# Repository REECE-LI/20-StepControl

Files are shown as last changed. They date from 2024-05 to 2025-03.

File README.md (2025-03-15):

# 20步进电机闭环驱动



## 项目来源

项目参考了[XDrive](https://github.com/unlir/XDrive)和[稚晖君的Dummy](https://github.com/peng-zhihui/Dummy-Robot)内部的20步进电机工程。

固件是在稚晖君42步进电机（与20电机通用）的程序上改进的。

## 更新部分

此处与稚晖君版本的作比较。

1. MCU部分由STM32F103CBT6更换为STM32F303CCT6。

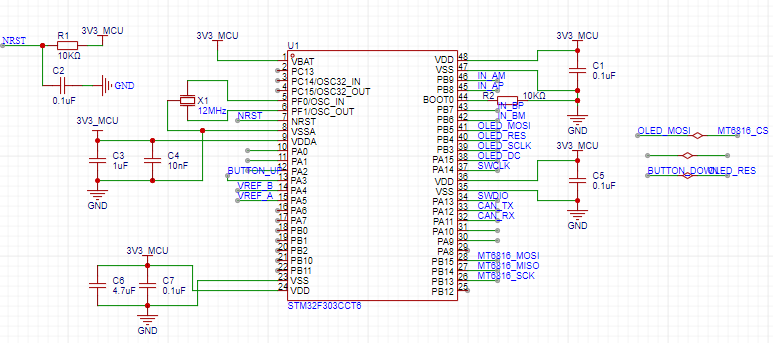
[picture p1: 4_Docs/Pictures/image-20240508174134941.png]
   

   - 内部flash翻倍（现在是256KB），原版的128KB在使用新版的`gcc`编译的时候会内存溢出（由于磁编码器需要校准，占用了32KB）。
   - 驱动器的电压控制直接使用DAC生成，不使用二阶低通滤波，硬件减少。
   - 由于flash翻倍了，可以在42步进电机上面增加一块Oled屏幕（XDrive上面有一块Oled屏幕，稚晖君版本上面预留了Oled的接口，但是flash已经完全用完了）。

2. DCDC部分直接降压到3.3V，取消LDO

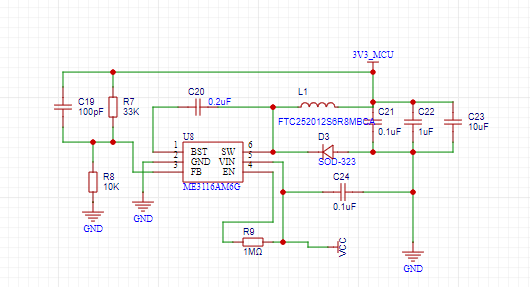
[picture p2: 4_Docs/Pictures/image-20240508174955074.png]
   

   - 没啥好说的。。。我就是懒得再焊LDO
   - Boost的自举电容需要0.2uF以上，原版使用了两个0402-0.1uF并联，这里直接使用0603-0.22uF，所占用面积差不多。
   - 分压电阻那可以再精细一点，当前输出的电压大约是3.4V。

3. CAN芯片由TJA1050更换为SIT3051

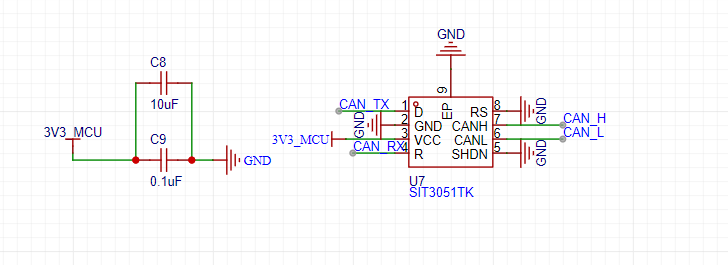
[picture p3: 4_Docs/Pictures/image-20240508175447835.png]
   

   - 小且便宜

## 使用

固件是在稚晖君的固件上面进行修改，使用Clion进行的烧写。（[Clion的教程在这里](https://zhuanlan.zhihu.com/p/145801160)）下载接口、电源接口、CAN接口都是焊盘连接。

- 按键按下通电程序会自动进行校准，校准完成后按下按键进入位置闭环，自动归零。
- 拨动开关是CAN信号120Ω的开关。
- 校准完后，我使用的是稚晖君的UltraLink里面的步进电机调试器，进行位置和速度的查看。（42步进电机版本加上了Oled屏幕可以直接查看）

- CAN信号控制指令可以在`can_base.cpp`中查看（如果有需要之后可以更新一下）

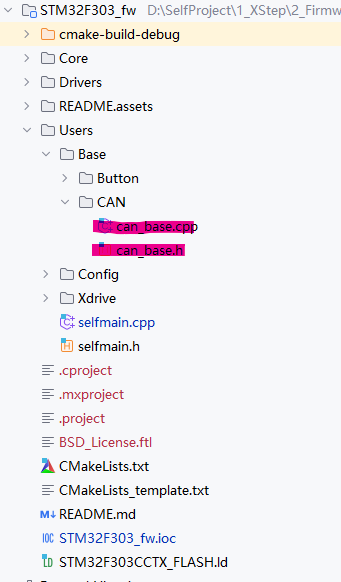
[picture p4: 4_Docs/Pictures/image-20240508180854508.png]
  

- 附一张42步进电机的驱动板，市面上的42步进闭环驱动其实很丰富了，张大头和创客都做的很好，后续再开（肯定不是因为懒）

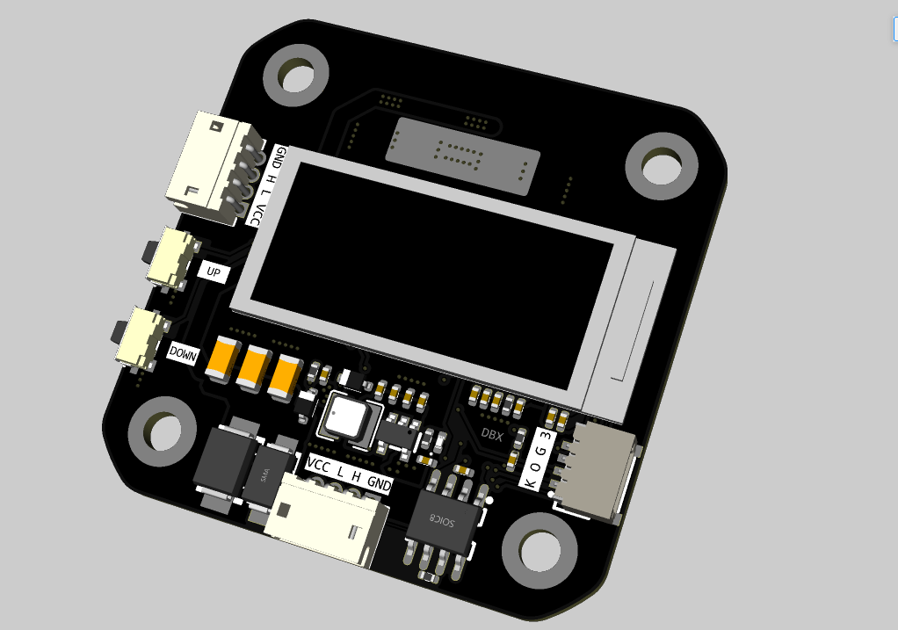
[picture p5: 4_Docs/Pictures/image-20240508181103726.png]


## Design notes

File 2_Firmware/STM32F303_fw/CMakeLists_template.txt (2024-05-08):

#THIS FILE IS AUTO GENERATED FROM THE TEMPLATE! DO NOT CHANGE!
set(CMAKE_SYSTEM_NAME Generic)
set(CMAKE_SYSTEM_VERSION 1)
cmake_minimum_required(VERSION 3.27)

# specify cross-compilers and tools
set(CMAKE_C_COMPILER arm-none-eabi-gcc)
set(CMAKE_CXX_COMPILER arm-none-eabi-g++)
set(CMAKE_ASM_COMPILER  arm-none-eabi-gcc)
set(CMAKE_AR arm-none-eabi-ar)
set(CMAKE_OBJCOPY arm-none-eabi-objcopy)
set(CMAKE_OBJDUMP arm-none-eabi-objdump)
set(SIZE arm-none-eabi-size)
set(CMAKE_TRY_COMPILE_TARGET_TYPE STATIC_LIBRARY)

# project settings
project(STM32F303_fw C CXX ASM)
set(CMAKE_CXX_STANDARD 17)
set(CMAKE_C_STANDARD 11)

#Uncomment for hardware floating point
#add_compile_definitions(ARM_MATH_CM4;ARM_MATH_MATRIX_CHECK;ARM_MATH_ROUNDING)
#add_compile_options(-mfloat-abi=hard -mfpu=fpv4-sp-d16)
#add_link_options(-mfloat-abi=hard -mfpu=fpv4-sp-d16)

#Uncomment for software floating point
#add_compile_options(-mfloat-abi=soft)

add_compile_options(-mcpu=cortex-m4 -mthumb -mthumb-interwork)
add_compile_options(-ffunction-sections -fdata-sections -fno-common -fmessage-length=0)

# uncomment to mitigate c++17 absolute addresses warnings
#set(CMAKE_CXX_FLAGS "${CMAKE_CXX_FLAGS} -Wno-register")

# Enable assembler files preprocessing
add_compile_options($<$<COMPILE_LANGUAGE:ASM>:-x$<SEMICOLON>assembler-with-cpp>)

if ("${CMAKE_BUILD_TYPE}" STREQUAL "Release")
    message(STATUS "Maximum optimization for speed")
    add_compile_options(-Ofast)
elseif ("${CMAKE_BUILD_TYPE}" STREQUAL "RelWithDebInfo")
    message(STATUS "Maximum optimization for speed, debug info included")
    add_compile_options(-Ofast -g)
elseif ("${CMAKE_BUILD_TYPE}" STREQUAL "MinSizeRel")
    message(STATUS "Maximum optimization for size")
    add_compile_options(-Os)
else ()
    message(STATUS "Minimal optimization, debug info included")
    add_compile_options(-Og -g)
endif ()

include_directories(Core/Inc Drivers/STM32F3xx_HAL_Driver/Inc
        Drivers/STM32F3xx_HAL_Driver/Inc/Legacy
        Drivers/CMSIS/Device/ST/STM32F3xx/Include
        Drivers/CMSIS/Include
        Users
        Users/Base/Button
        Users/Base/CAN
#        Users/Retarget
        Users/Xdrive
        Users/Xdrive/Driver
        Users/Xdrive/Encoder
        Users/Xdrive/Memory
        Users/Xdrive/Motor
        Users/Oled
)

add_definitions(-DDEBUG -DUSE_HAL_DRIVER -DSTM32F303xC)

file(GLOB_RECURSE SOURCES "Core/*.*" "Drivers/*.*" "Users/*.*")

set(LINKER_SCRIPT ${CMAKE_SOURCE_DIR}/STM32F303CCTX_FLASH.ld)

add_link_options(-Wl,-gc-sections,--print-memory-usage,-Map=${PROJECT_BINARY_DIR}/${PROJECT_NAME}.map)
add_link_options(-mcpu=cortex-m4 -mthumb -mthumb-interwork)
add_link_options(-T ${LINKER_SCRIPT})

add_executable(${PROJECT_NAME}.elf ${SOURCES} ${LINKER_SCRIPT})

set(HEX_FILE ${PROJECT_BINARY_DIR}/${PROJECT_NAME}.hex)
set(BIN_FILE ${PROJECT_BINARY_DIR}/${PROJECT_NAME}.bin)

add_custom_command(TARGET ${PROJECT_NAME}.elf POST_BUILD
        COMMAND ${CMAKE_OBJCOPY} -Oihex $<TARGET_FILE:${PROJECT_NAME}.elf> ${HEX_FILE}
        COMMAND ${CMAKE_OBJCOPY} -Obinary $<TARGET_FILE:${PROJECT_NAME}.elf> ${BIN_FILE}
        COMMENT "Building ${HEX_FILE}
Building ${BIN_FILE}")

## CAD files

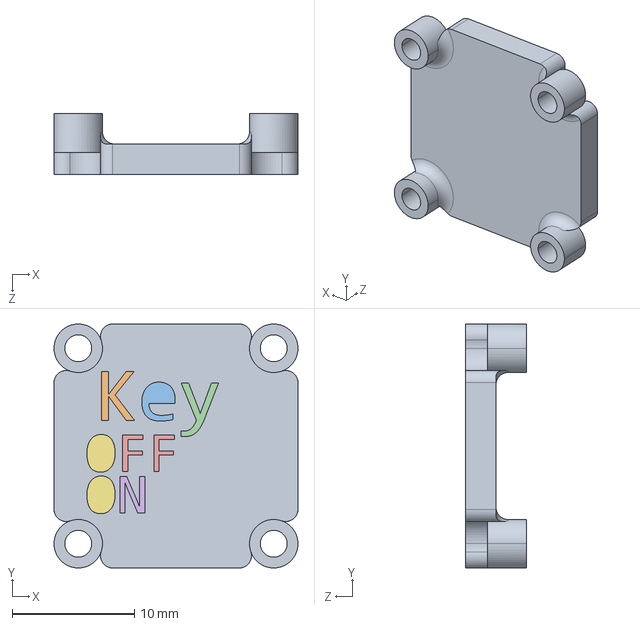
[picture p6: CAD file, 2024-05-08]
3_3Dmodels/20步进背板.STEP
20.0 x 20.0 x 5.00 mm

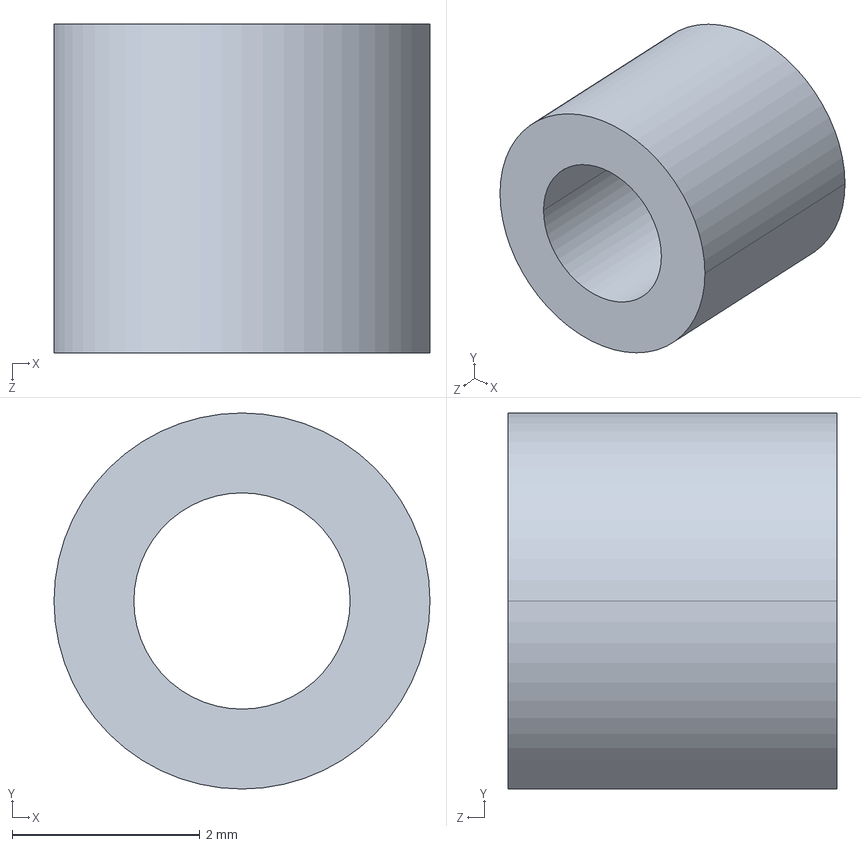
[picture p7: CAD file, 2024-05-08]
3_3Dmodels/20步进增高.STEP
4.00 x 4.00 x 3.50 mm

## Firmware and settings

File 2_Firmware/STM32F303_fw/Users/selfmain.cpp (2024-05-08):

#include "selfmain.h"


#include <cstdio>

#include "mt6816_stm32.h"
#include "tb67h450_stm32.h"

#include "button_stm32.h"
#include "configurations.h"
#include "can_base.h"


#include "encoder_calibrator_stm32.h"
#include "stockpile_f303cc.h"
#include "stockpile_config.h"


/*
TIM2通道 3 4进行DAC
TIM3 进行20kHZ中断
PB12 BTN_DOWN Key_1
 */

BoardConfig_t boardConfig;

Motor motor;
TB67H450 tb67H450;
MT6816 mt6816;
EncoderCalibrator encoderCalibrator(&motor);
Button button1(1, 1000);

void OnButton1Event(Button::Event _event);

void OnButton2Event(Button::Event _event);

void SelfMain() {

    //  读取配置 当前没有写
//    Stockpile_Flash_Data_Read_Data(&stockpile_data, &boardConfig, sizeof(BoardConfig_t));
    // use flash
    if (boardConfig.configStatus != CONFIG_OK) // use default settings
    {
        boardConfig = BoardConfig_t{
                .configStatus = CONFIG_OK,
                .canNodeId = 1,
                .encoderHomeOffset = 0,
                .defaultMode = Motor::MODE_COMMAND_VELOCITY,
                .currentLimit = 1 * 1000,    // A
                .velocityLimit = 1600 * motor.MOTOR_ONE_CIRCLE_SUBDIVIDE_STEPS, // r/s
                .velocityAcc = 100 * motor.MOTOR_ONE_CIRCLE_SUBDIVIDE_STEPS,   // r/s^2
                .calibrationCurrent=800,
                .dce_kp = 200,
                .dce_kv = 80,
                .dce_ki = 300,
                .dce_kd = 250,
                .enableMotorOnBoot=false,
                .enableStallProtect=false
        };

        Stockpile_Flash_Data_Write_Data16(&stockpile_data, (uint16_t *) &boardConfig, sizeof(BoardConfig_t));
    }
    // 加载板载数据
    motor.config.motionParams.encoderHomeOffset = boardConfig.encoderHomeOffset;
    motor.config.motionParams.ratedCurrent = boardConfig.currentLimit;
    motor.config.motionParams.ratedVelocity = boardConfig.velocityLimit;
    motor.config.motionParams.ratedVelocityAcc = boardConfig.velocityAcc;
    motor.motionPlanner.velocityTracker.SetVelocityAcc(boardConfig.velocityAcc);
    motor.motionPlanner.positionTracker.SetVelocityAcc(boardConfig.velocityAcc);
    motor.config.motionParams.caliCurrent = boardConfig.calibrationCurrent;
    motor.config.ctrlParams.dce.kp = boardConfig.dce_kp;
    motor.config.ctrlParams.dce.kv = boardConfig.dce_kv;
    motor.config.ctrlParams.dce.ki = boardConfig.dce_ki;
    motor.config.ctrlParams.dce.kd = boardConfig.dce_kd;
    motor.config.ctrlParams.stallProtectSwitch = boardConfig.enableStallProtect;

    /*---------------- Init Motor ----------------*/
    motor.AttachDriver(&tb67H450);
    motor.AttachEncoder(&mt6816);
    motor.controller->Init();
    motor.driver->Init();
    motor.encoder->Init();

    /*------------- Init peripherals -------------*/
    button1.SetOnEventListener(OnButton1Event);


    /*------- Start Close-Loop Control Tick ------*/
    CANInit(&hcan);
//    HAL_Delay(1);
    HAL_TIM_Base_Start_IT(&htim4);  // 100Hz
    HAL_TIM_Base_Start_IT(&htim3);  // 20kHz
//    HAL_Delay(1);
//
    if (button1.IsPressed() )
        encoderCalibrator.isTriggered = true;
    // 测试使用


    for (;;) {
        encoderCalibrator.TickMainLoop();
        if (boardConfig.configStatus == CONFIG_COMMIT) {
            boardConfig.configStatus = CONFIG_OK;
            // eeprom.put(0, boardConfig);
        } else if (boardConfig.configStatus == CONFIG_RESTORE) {
            // eeprom.put(0, boardConfig);
            HAL_NVIC_SystemReset();
        }

    }
}

void HAL_TIM_PeriodElapsedCallback(TIM_HandleTypeDef *htim) {
    if (htim->Instance == TIM3) {

        if (encoderCalibrator.isTriggered)
            encoderCalibrator.Tick20kHz();
        else
            motor.Tick20kHz();
    } else if (htim->Instance == TIM4) {
        button1.Tick(10);


    }
}


// button event
void OnButton1Event(Button::Event _event) {
    switch (_event) {
        case ButtonBase::UP:
            break;
        case ButtonBase::DOWN:
            break;
        case ButtonBase::LONG_PRESS:
//            HAL_NVIC_SystemReset();
            break;
        case ButtonBase::CLICK:
            motor.controller->SetCtrlMode(Motor::MODE_COMMAND_POSITION);
            break;
    }
}

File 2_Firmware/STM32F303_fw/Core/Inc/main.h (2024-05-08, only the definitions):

#define BUTTON_UP_Pin GPIO_PIN_3
#define BUTTON_UP_GPIO_Port GPIOA
#define VREF_A_Pin GPIO_PIN_4
#define VREF_A_GPIO_Port GPIOA
#define VREF_B_Pin GPIO_PIN_5
#define VREF_B_GPIO_Port GPIOA
#define MT6818_CLK_Pin GPIO_PIN_13
#define MT6818_CLK_GPIO_Port GPIOB
#define MT6816_MISO_Pin GPIO_PIN_14
#define MT6816_MISO_GPIO_Port GPIOB
#define MT6818_MOSI_Pin GPIO_PIN_15
#define MT6818_MOSI_GPIO_Port GPIOB
#define MT6816_CS_Pin GPIO_PIN_5
#define MT6816_CS_GPIO_Port GPIOB
#define BM_Pin GPIO_PIN_6
#define BM_GPIO_Port GPIOB
#define BP_Pin GPIO_PIN_7
#define BP_GPIO_Port GPIOB
#define AP_Pin GPIO_PIN_8
#define AP_GPIO_Port GPIOB
#define AM_Pin GPIO_PIN_9
#define AM_GPIO_Port GPIOB

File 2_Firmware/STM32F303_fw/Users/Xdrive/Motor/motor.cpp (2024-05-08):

#include "configurations.h"
#include "motor.h"

#include <cmath>


void Motor::Tick20kHz() {
    // 1.Encoder data Update
    encoder->UpdateAngle();

    // 2.Motor Control Update
    CloseLoopControlTick();
}


void Motor::AttachEncoder(EncoderBase *_encoder) {
    encoder = _encoder;
}


void Motor::AttachDriver(DriverBase *_driver) {
    driver = _driver;
}


void Motor::CloseLoopControlTick() {
    /************************************ First Called ************************************/
    static bool isFirstCalled = true;
    if (isFirstCalled) {
        int32_t angle;
        if (config.motionParams.encoderHomeOffset < MOTOR_ONE_CIRCLE_SUBDIVIDE_STEPS / 2) {
            angle =
                    encoder->angleData.rectifiedAngle >
                    config.motionParams.encoderHomeOffset + MOTOR_ONE_CIRCLE_SUBDIVIDE_STEPS / 2 ?
                    encoder->angleData.rectifiedAngle - MOTOR_ONE_CIRCLE_SUBDIVIDE_STEPS :
                    encoder->angleData.rectifiedAngle;
        } else {
            angle =
                    encoder->angleData.rectifiedAngle <
                    config.motionParams.encoderHomeOffset - MOTOR_ONE_CIRCLE_SUBDIVIDE_STEPS / 2 ?
                    encoder->angleData.rectifiedAngle + MOTOR_ONE_CIRCLE_SUBDIVIDE_STEPS :
                    encoder->angleData.rectifiedAngle;
        }

        controller->realLapPosition = angle;
        controller->realLapPositionLast = angle;
        controller->realPosition = angle;
        controller->realPositionLast = angle;

        isFirstCalled = false;
        return;
    }

    /********************************* Update Data *********************************/
    int32_t deltaLapPosition;

    // Read Encoder data
    controller->realLapPositionLast = controller->realLapPosition;
    controller->realLapPosition = encoder->angleData.rectifiedAngle;

    // Lap-Position calculate
    deltaLapPosition = controller->realLapPosition - controller->realLapPositionLast;
    if (deltaLapPosition > MOTOR_ONE_CIRCLE_SUBDIVIDE_STEPS >> 1)
        deltaLapPosition -= MOTOR_ONE_CIRCLE_SUBDIVIDE_STEPS;
    else if (deltaLapPosition < -MOTOR_ONE_CIRCLE_SUBDIVIDE_STEPS >> 1)
        deltaLapPosition += MOTOR_ONE_CIRCLE_SUBDIVIDE_STEPS;

    // Naive-Position calculate
    controller->realPositionLast = controller->realPosition;
    controller->realPosition += deltaLapPosition;

    /********************************* Estimate Data *********************************/
    // Estimate Velocity
    controller->estVelocityIntegral += (
            (controller->realPosition - controller->realPositionLast) * motionPlanner.CONTROL_FREQUENCY
            + ((controller->estVelocity << 5) - controller->estVelocity)
    );
    controller->estVelocity = controller->estVelocityIntegral >> 5;
    controller->estVelocityIntegral -= (controller->estVelocity << 5);

    // Estimate Position
    controller->estLeadPosition = Controller::CompensateAdvancedAngle(controller->estVelocity);
    controller->estPosition = controller->realPosition + controller->estLeadPosition;

    // Estimate Error
    controller->estError = controller->softPosition - controller->estPosition;

    /************************************ Ctrl Loop ************************************/
    if (controller->isStalled ||
        controller->softDisable ||
        !encoder->IsCalibrated()) {
        controller->ClearIntegral();    // clear integrals
        controller->focPosition = 0;    // clear outputs
        controller->focCurrent = 0;
        driver->Sleep();
    } else if (controller->softBrake) {
        controller->ClearIntegral();
        controller->focPosition = 0;
        controller->focCurrent = 0;
        driver->Brake();
    } else {
        switch (controller->modeRunning) {
            case MODE_STEP_DIR:
                controller->CalcDceToOutput(controller->softPosition, controller->softVelocity);
                break;
            case MODE_STOP:
                driver->Sleep();
                break;
            case MODE_COMMAND_Trajectory:
                controller->CalcDceToOutput(controller->softPosition, controller->softVelocity);
                break;
            case MODE_COMMAND_CURRENT:
                controller->CalcCurrentToOutput(controller->softCurrent);
                break;
            case MODE_COMMAND_VELOCITY:
                controller->CalcPidToOutput(controller->softVelocity);
                break;
            case MODE_COMMAND_POSITION:
                controller->CalcDceToOutput(controller->softPosition, controller->softVelocity);
                break;
            case MODE_PWM_CURRENT:
                controller->CalcCurrentToOutput(controller->softCurrent);
                break;
            case MODE_PWM_VELOCITY:
                controller->CalcPidToOutput(controller->softVelocity);
                break;
            case MODE_PWM_POSITION:
                controller->CalcDceToOutput(controller->softPosition, controller->softVelocity);
                break;
            default:
                break;
        }
    }

    /******************************* Mode Change Handle *******************************/
    if (controller->modeRunning != controller->requestMode) {
        controller->modeRunning = controller->requestMode;
        controller->softNewCurve = true;
    }

    /******************************* Update Hard-Goal *******************************/
    if (controller->goalVelocity > config.motionParams.ratedVelocity)
        controller->goalVelocity = config.motionParams.ratedVelocity;
    else if (controller->goalVelocity < -config.motionParams.ratedVelocity)
        controller->goalVelocity = -config.motionParams.ratedVelocity;
    if (controller->goalCurrent > config.motionParams.ratedCurrent)
        controller->goalCurrent = config.motionParams.ratedCurrent;
    else if (controller->goalCurrent < -config.motionParams.ratedCurrent)
        controller->goalCurrent = -config.motionParams.ratedCurrent;

    /******************************** Motion Plan *********************************/
    if ((controller->softDisable && !controller->goalDisable) ||
        (controller->softBrake && !controller->goalBrake)) {
        controller->softNewCurve = true;
    }

    if (controller->softNewCurve) {
        controller->softNewCurve = false;
        controller->ClearIntegral();
        controller->ClearStallFlag();
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

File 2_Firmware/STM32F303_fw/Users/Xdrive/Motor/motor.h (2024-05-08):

#ifndef CTRL_STEP_FW_MOTOR_H
#define CTRL_STEP_FW_MOTOR_H

#include "motion_planner.h"
#include "encoder_base.h"
#include "driver_base.h"


#ifdef __cplusplus
extern "C" {
#endif


class Motor
{
public:
    Motor() :
        controller(&controllerInstance)
    {
        /****************** Default Configs *******************/
        config.motionParams.encoderHomeOffset = 0;
        config.motionParams.caliCurrent = 2000;             // (mA)
        config.motionParams.ratedCurrent = 1000;            // (mA)
        config.motionParams.ratedCurrentAcc = 2 * 1000;     // (mA/s)
        config.motionParams.ratedVelocity = 30 * MOTOR_ONE_CIRCLE_SUBDIVIDE_STEPS;
        config.motionParams.ratedVelocityAcc = 1000 * MOTOR_ONE_CIRCLE_SUBDIVIDE_STEPS;

        config.ctrlParams.stallProtectSwitch = false;
        config.ctrlParams.pid =
            Controller::PID_t{
                .kp = 5,
                .ki = 30,
                .kd = 0
            };
        config.ctrlParams.dce =
            Controller::DCE_t{
                .kp = 200,
                .kv = 80,
                .ki = 300,
                .kd = 250
            };

        /*****************************************************/


        motionPlanner.AttachConfig(&config.motionParams);
        controller->AttachConfig(&config.ctrlParams);
    }


    const int32_t MOTOR_ONE_CIRCLE_HARD_STEPS = 200; // for 1.8° step-motors
    const int32_t SOFT_DIVIDE_NUM = 256;
    const int32_t MOTOR_ONE_CIRCLE_SUBDIVIDE_STEPS = MOTOR_ONE_CIRCLE_HARD_STEPS * SOFT_DIVIDE_NUM;

    typedef enum
    {
        MODE_STOP,
        MODE_COMMAND_POSITION,
        MODE_COMMAND_VELOCITY,
        MODE_COMMAND_CURRENT,
        MODE_COMMAND_Trajectory,
        MODE_PWM_POSITION,
        MODE_PWM_VELOCITY,
        MODE_PWM_CURRENT,
        MODE_STEP_DIR,
    } Mode_t;

    typedef enum
    {
        STATE_STOP,
        STATE_FINISH,
        STATE_RUNNING,
        STATE_OVERLOAD,
        STATE_STALL,
        STATE_NO_CALIB
    } State_t;


    class Controller
    {
    public:
        friend Motor;

        typedef struct
        {
            bool kpValid, kiValid, kdValid;
            int32_t kp, ki, kd;
            int32_t vError, vErrorLast;
            int32_t outputKp, outputKi, outputKd;
            int32_t integralRound;
            int32_t integralRemainder;
            int32_t output;
        } PID_t;

        typedef struct
        {
            int32_t kp, kv, ki, kd;
            int32_t pError, vError;
            int32_t outputKp, outputKi, outputKd;
            int32_t integralRound;
            int32_t integralRemainder;
            int32_t output;
        } DCE_t;

        typedef struct
        {
            PID_t pid;
            DCE_t dce;

            bool stallProtectSwitch;
        } Config_t;


        explicit Controller(Motor* _context)
        {
            context = _context;

            requestMode = MODE_STOP;
            modeRunning = MODE_STOP;
        }


        Config_t* config = nullptr;
        Mode_t requestMode;
        Mode_t modeRunning;
        State_t state = STATE_STOP;
        bool isStalled = false;


        void Init();
        void SetCtrlMode(Mode_t _mode);
        void SetCurrentSetPoint(int32_t _cur);
        void SetVelocitySetPoint(int32_t _vel);
        void SetPositionSetPoint(int32_t _pos);
        bool SetPositionSetPointWithTime(int32_t _pos, float _time);
        float GetPosition(bool _isLap = false);
        float GetVelocity();
        float GetFocCurrent();
        void AddTrajectorySetPoint(int32_t _pos, int32_t _vel);
        void SetDisable(bool _disable);
        void SetBrake(bool _brake);
        void ApplyPosAsHomeOffset();
        void ClearStallFlag();


    private:
        Motor* context;
        int32_t realLapPosition{};
        int32_t realLapPositionLast{};
        int32_t realPosition{};
        int32_t realPositionLast{};
        int32_t estVelocity{};
        int32_t estVelocityIntegral{};
        int32_t estLeadPosition{};
        int32_t estPosition{};
        int32_t estError{};
        int32_t focCurrent{};
        int32_t goalPosition{};
        int32_t goalVelocity{};
        int32_t goalCurrent{};
        bool goalDisable{};
        bool goalBrake{};
        int32_t softPosition{};
        int32_t softVelocity{};
        int32_t softCurrent{};
        bool softDisable{};
        bool softBrake{};
        bool softNewCurve{};
        int32_t focPosition{};
        uint32_t stalledTime{};
        uint32_t overloadTime{};
        bool overloadFlag{};


        void AttachConfig(Config_t* _config);
        void CalcCurrentToOutput(int32_t current);
        void CalcPidToOutput(int32_t _speed);
        void CalcDceToOutput(int32_t _location, int32_t _speed);
        void ClearIntegral() const;

        static int32_t CompensateAdvancedAngle(int32_t _vel);
    };


    struct Config_t
    {
        MotionPlanner::Config_t motionParams{};
        Controller::Config_t ctrlParams{};
    };
    Config_t config;

    MotionPlanner motionPlanner;
    Controller* controller = nullptr;
    EncoderBase* encoder = nullptr;
    DriverBase* driver = nullptr;


    void Tick20kHz();
    void AttachEncoder(EncoderBase* _encoder);
    void AttachDriver(DriverBase* _driver);


private:
    Controller controllerInstance = Controller(this);


    void CloseLoopControlTick();
};
#ifdef __cplusplus
}
/*---------------------------- C++ Scope ---------------------------*/

#endif


#endif

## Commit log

2024-05-08 20步进电机闭环驱动开源
    [20步进增高.STEP, 20步进背板.STEP, DapLink.cfg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]
2024-05-08 删除了原内部md文件
2025-03-15 Update README.md
    单片机名字打错了

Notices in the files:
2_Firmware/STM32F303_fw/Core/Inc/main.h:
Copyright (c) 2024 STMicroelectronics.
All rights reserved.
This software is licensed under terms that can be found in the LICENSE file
